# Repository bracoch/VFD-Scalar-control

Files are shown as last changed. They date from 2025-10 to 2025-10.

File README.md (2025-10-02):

Frequency Converter Design – Final Thesis Project
📌 Overview

This project was developed as part of my final thesis in Electrical Engineering.
The goal was to design and implement a complete frequency converter for asynchronous motor control, covering the full engineering cycle from concept to validation.

⚙️ Key Features

Power Stage Design – dimensioning of rectifier, DC link, and inverter section

Control Algorithms – PWM generation, Scalar V/f control

System Simulation – MATLAB/Simulink models for power electronics

Hardware Prototyping – schematic design and PCB layout

Testing & Validation – practical measurements, analysis and performance

🛠️ Technologies Used

MATLAB/Simulink – modeling and simulation

ISIS / Proteus - modeling and simulation

EasyEda PCB – schematic capture and PCB design

Arduino – microcontroller control logic

Oscilloscope & Measurement Tools – signal and harmonic analysis

📊 Results

Achieved SCALAR V/F stable motor control from 0–70 Hz

Verified power stage design through thermal and efficiency measurements

Implemented protection features (overcurrent, undervoltage, overvoltage)

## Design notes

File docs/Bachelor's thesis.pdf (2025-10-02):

## Faculty of Technical Sciences in Čačak

## University of Kragujevac

# Scalar Control of Three-Phase Induction Motor Characteristics

## Bachelor Thesis

Aleksandar Brakocevic | Thesis Supervisor
1220/17 | PhD Milan Dobricic

___________________________ ___________________________

SUMMARY

Alternating current (AC) motors are usually controlled by variable frequency drives (VFD), which regulate motor speed by adjusting the frequency of the supply voltage. Depending on the application and the required level of speed regulation, VFDs can be controlled using scalar or vector methods. The most common type of VFD control is scalar, which applies the volts-per-hertz (V/Hz) or volts-per-frequency (V/F) method.
The terms variable frequency drive (VFD) and variable speed drive (VSD) are often used interchangeably, but there is a difference between the two. A variable speed drive (VSD) is any drive that can control the speed of a piece of equipment, including both AC and DC motors. VSDs may operate through mechanical, hydraulic, or electrical drives. A variable frequency drive (VFD), on the other hand, is specifically used to control the speed of AC motors by varying the frequency of the motor supply voltage.
How does V/Hz control work?
AC motors are designed to operate with a constant magnetic field (flux). The strength of this magnetic field is proportional to the ratio of voltage (V) to frequency (Hz), or V/Hz. The VFD controls the motor speed by varying the frequency of the applied voltage, according to the synchronous speed equation:

Ns =

120 ∗ f
p
where:
- ns= synchronous speed (in revolutions per minute, rpm)
- f = supply frequency (in hertz, Hz)
- P = number of motor poles

Changing the frequency of the voltage affects both the motor speed and the strength of the magnetic field. When the frequency is reduced (for lower motor speeds), the magnetic field increases, creating excessive heat. When the frequency is increased (for higher motor speeds), the magnetic field decreases, resulting in lower torque. To maintain a constant magnetic flux, the V/Hz ratio must remain constant. The V/Hz method keeps torque generation stable regardless of frequency. V/Hz control of a VFD avoids changes in the strength of the magnetic field by adjusting the voltage together with the frequency so that the V/Hz ratio remains constant.

The appropriate V/Hz ratio is determined by the rated voltage and frequency of the motor. For example, a motor rated for delta connection at 230 V and 50 Hz will always operate best with a V/Hz ratio of 4.6 (230/50 = 4.6).

Open-loop (V/Hz) control does not use feedback and only adjusts the voltage and frequency of the motor based on an external speed command.
Closed-loop V/Hz control can incorporate encoder feedback to measure the actual motor speed. An error signal is generated based on the difference between the actual speed and the reference speed, and the controller produces a new frequency command to compensate for the error. Although closed-loop V/Hz improves speed regulation, it is not commonly used because of the additional cost and complexity of the feedback hardware.

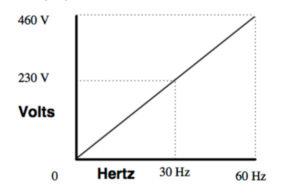
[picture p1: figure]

Figure 1.
V/Hz regulation maintains a constant ratio between voltage (V) and frequency (Hz).

V/Hz control is a simple and low-cost method for operating variable frequency drives and is generally considered the most common VFD control scheme. It is suitable for both constant-torque and variable-torque applications and can provide up to 150 percent of rated torque at zero speed for starting and peak loads. Speed regulation is typically within 2 to 3 percent of the maximum rated frequency, making this method unsuitable for applications where precise speed control is critical.

The most common use of V/Hz control is for driving industrial equipment such as fans and compressors. A unique advantage of V/Hz control over other methods is that it allows multiple motors to be operated from a single VFD. All motors will start and stop simultaneously and run at the same speed, which is beneficial in some process applications such as heating and cooling.

Contents:

6. Microcontroller Program | Error! Bookmark not defined.
6.2 Program Flow | Error! Bookmark not defined.

Appendix 1. Output Stage Schematic | Error! Bookmark not defined.

Appendix 4. Printed Circuit Board Layout (Top Side)* .... Error! Bookmark not defined.

Appendix 10. Parts List | Error! Bookmark not defined.

### 1. PREFACE

The final thesis represents a seal on the previously acquired knowledge that was selflessly imparted to us by our professors during lectures. Likewise, this work I have chosen to pursue is an attempt to leave a positive impression on the professors and to justify the time they dedicated to us, striving to bring us closer to the subject matter and prepare us for future endeavors.
I have spent a great deal of time working on this thesis, but that time is nothing compared to the knowledge I have gained, both theoretical and especially practical, during its realization. Each stage of the work brought new positive experiences as well as disappointments, particularly when things did not go the way I had hoped. As the saying goes: “Electronic components run on white smoke—when the smoke escapes, the component no longer works.” I too have witnessed plenty of white smoke, but perseverance paid off, and I successfully completed the project. The feeling and satisfaction of having accomplished something independently and with full understanding is unparalleled.
I would like to express my deep gratitude to Professor Dr. Milan Dobričić, Professor Dr. Dragan Brajović, and Professor Dr. Božimir Mišković.

Aleksandar Brakočević
September 2021

### 1.1 INTRODUCTION

Induction motors are the most commonly used motors. They are robust, reliable, and durable. When voltage is applied to an induction motor according to the specifications on its nameplate, the motor runs at its rated speed. However, in many applications, variable speed operation is required. For example, a washing machine may use different speeds for each wash cycle. Historically, mechanical gear and belt systems were used to achieve variable speeds. Thanks to the rapid advancement of electronics, power and control systems have matured to the point where these components are now used to control motors instead of mechanical gears. Electronics not only control motor speed but can also improve the dynamic performance of the motor. Additionally, electronics can reduce the system’s average power consumption and lower motor noise.
Controlling an induction motor is complex because of its nonlinear characteristics. Although different control methods exist, the variable voltage variable frequency (VV/VF) or V/F method is the most common speed control method in open-loop systems. This method is most suitable for applications that do not require position control or high-precision speed regulation. Examples include heating, air conditioning, fans, and compressors.
V/F control can be implemented using inexpensive microcontrollers instead of costly processors and digital signal processors (DSP). Many microcontrollers have built-in hardware PWM (pulse width modulation) signal generators. The Arduino Mega development board is equipped with an ATmega2560 microcontroller, which contains six timers and fifteen PWM pins that can be configured in the corresponding registers for different signal values. In this work, we use three PWM pins to generate three SPWM (sine pulse width modulation) signals phase-shifted by 120°.

This thesis covers the basics of scalar control of three-phase induction motors.

### 1.2 Nameplate

A typical nameplate (Figure 1) of an induction motor contains the following parameters:
- Rated supply voltage at the terminals in volts (V)
- Supply frequency in hertz (Hz)
- Rated current in amperes (A)
- Base speed in revolutions per minute (RPM)
- Power in watts or horsepower (kW–HP)
- Rated torque in newton-meters (Nm)
- Slip speed in RPM, or slip frequency in hertz (Hz)
- Type of winding insulation – class A, B, F, or H
- Efficiency
- Type of stator connection (for three-phase motors only), star (Y) or delta (Δ)

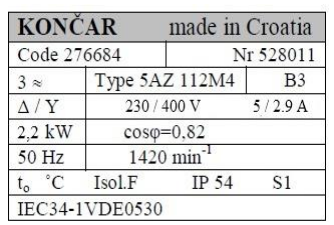
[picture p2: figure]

Figure 1. Motor Nameplate

### 1.3 Operating Principle of the Induction Motor

When rated alternating current supply is applied to the stator windings, a magnetic flux of constant magnitude is generated, rotating at synchronous speed. The rotating field moves in the air gap and closes through the stator and rotor, which induces corresponding electromotive forces in the conductors. In the stator winding, a counter electromotive force EsE is generated, which balances the applied stator voltage U. An electromotive force is also induced in the rotor winding. If the rotor circuit is closed, a current Ir will flow, whose active component has the same direction as the induced electromotive force. Since the conductor carrying the current IrI is located in a magnetic field, an electromagnetic force F acts on it, causing the rotor to turn in the direction of the rotating magnetic field. The sum of all the forces acting on the rotor conductors represents the electromagnetic torque of the motor.
As energy is transferred from the stator to the rotor by electromagnetic induction, asynchronous machines are often called induction machines. The windings are of resistive-inductive nature. Reactive energy is required to magnetize the magnetic material and the air gap between the stator and rotor. Since the asynchronous machine cannot generate reactive energy, it must draw it from the network. The current driven through the windings by the supply voltage will always be inductive. Therefore, the asynchronous machine, both in motor and generator mode, consumes reactive energy, which is one of the main reasons why it is used primarily as a motor. In generator mode, the asynchronous machine is used within autonomous power systems, where the reactive energy is supplied by a capacitor bank. In large industrial consumers with many high-power asynchronous motors, static compensators (usually capacitor banks) are often installed to improve the power factor so that reactive energy is not drawn from the network.
To reduce the relative speed, the rotor begins to rotate in the same direction as the flux and attempts to catch up. But in practice, the rotor can never “reach” the stator field. Thus, the rotor always runs slower than the speed of the stator field. This difference in speed is called slip speed, and it depends on the mechanical load on the motor shaft.
The frequency and speed of the motor, with respect to the input supply, are referred to as the synchronous frequency and synchronous speed. The synchronous speed is directly proportional to the ratio of the supply frequency to the number of poles in the motor. The synchronous speed of the induction motor is shown in Equation (1.1).

synchronous speed Ns =

120 ∗f
p
f – rated supply frequency | (1.1)
p – number of poles

Synchronous speed is the speed at which the stator flux rotates. The rotor flux rotates slower than the stator flux. This difference is called slip speed. The speed indicated on the motor nameplate is the base speed. Some manufacturers specify it as a percentage of synchronous speed, as shown in Equation (1.2):

Nk% =

(Ns−Nn) ∗100 Ns | (1.2)

where:
- Nn_= base speed
- Ns = synchronous speed
- Nk = slip speed

The slip percentage depends on the motor load: the higher the load, the greater the slip.

### 1.4 Types of asynchronous motors

Based on rotor construction, induction motors are classified into two categories:

- squirrel-cage motors
- slip-ring motors

The stator construction is the same for both types.

### 1.5 Squirrel-cage rotor motor

Almost 90% of asynchronous motors are squirrel-cage motors. This is because the squirrel-cage motor has a simple and robust construction. The rotor consists of a cylindrical laminated core with axially placed parallel slots to hold the conductors. Each slot is filled with copper, aluminum, or an alloy. The rotor bars are short-circuited by end rings on both sides, as shown in Figure 2. The rotor slots are not parallel to the shaft; they are skewed for two main reasons:

a) To ensure quiet motor operation by reducing magnetic noise.
b) To help reduce the tendency of the rotor to lock..

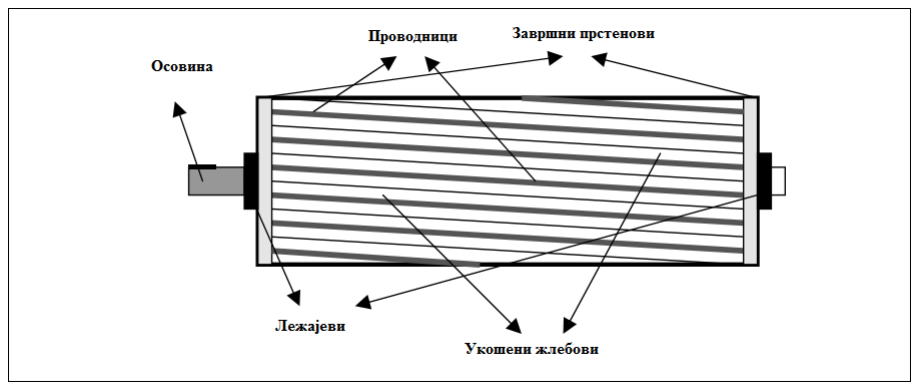
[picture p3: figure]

Figure 2. View of a squirrel-cage rotor

### 1.6 Slip-ring motor

The windings on the rotor are connected to three insulated slip rings on which brushes are mounted (Figure 3). This allows an external resistor to be introduced into the rotor winding. The external resistor can be used to increase the motor torque and modify the torque characteristics. Under normal operating conditions, the slip rings are short-circuited by an external switch. In normal conditions, the slip-ring motor operates like a squirrel-cage motor.

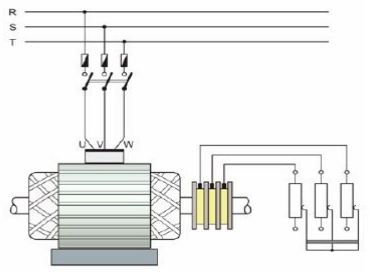
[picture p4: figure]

Figure 3. Slip-ring motor

### 1.7 Equivalent circuit of an asynchronous motor

The phasor model of the asynchronous motor, considering the steady-state motor quantities, is often used in the scalar control method. Before deriving the motor model, several assumptions are made:

- the stator windings are identical and sinusoidally distributed,
- the magnetic system is linear.

The voltage equations (2.1 and 2.2), with respect to the machine variables, can be expressed as:

V R I j s | s s | e s = | + ωλ | (2.1)
0 = | + R I j r r | | s r ωλ

Where Vs
| | | is the stator voltage vector,
s

I
is the stator current vector,

λs
is the stator leakage

flux vector,
r

I
is the instantaneous rotor current vector,

λr
is the rotor leakage flux vector,

ωe

is the synchronous speed,

ωr
is the rotor electrical speed, and
ω ω ω s | e | r
| =−
is the slip speed. | (2.2)

For a magnetically linear system, the leakage flux vector is calculated as follows (equations 2.3 and 2.4).
λs | s s | m r = | + L I L I
Stator leakage flux | (2.3)
λr | m s | r r = | + L I L I
Rotor leakage flux | (2.4)

In the above equations,

Rs
is the stator resistance,

Rr
is the rotor resistance,

mL
is the mutual

inductance,

s L
is the stator inductance, and

r L
is the rotor inductance.

In Figure 4, the equivalent circuit of the asynchronous motor is shown.

L | L L ls | s | m = | −
is the stator

leakage inductance,

L | L L lr | r | m = | −
is the rotor leakage inductance,, а s = ωs / ωe

/

### s e s =ωω

is

the | slip | ratio.

Figure 4. Equivalent circuit of the asynchronous motor

According to equations (3.1) ~ (3.4), the stator voltage and current are related by the equation:

( | )
( | )
( | )
2 | 2 | 2 | 2 2
2 | 2 2 | 2
s | e M | r | s | r | s | s r | r M
s | s | s | e s
r | s r | r | s r
LR | L R | L L | L L
V | R | I | j | I
R | L | R | L
ωω | ω
ω
| ω | | | | | ω
æ | ö | + | −
= | + | + ç | ÷ ç | ÷ + | + è | ø
(2.5)

And the stator leakage flux can be expressed as:
( | )
( | )
2 | 2 | 2 | 2

2 2

s | r | s | s r | r M | s | r M
s | s
r | r | s
L R | L L | L L | j R L
I
| R | L
ω | ω
λ
ω
+ | − | −
=
| +

(2.6)

Figure 5 shows the vector diagram of the motor quantities when the asynchronous motor operates in motoring mode..

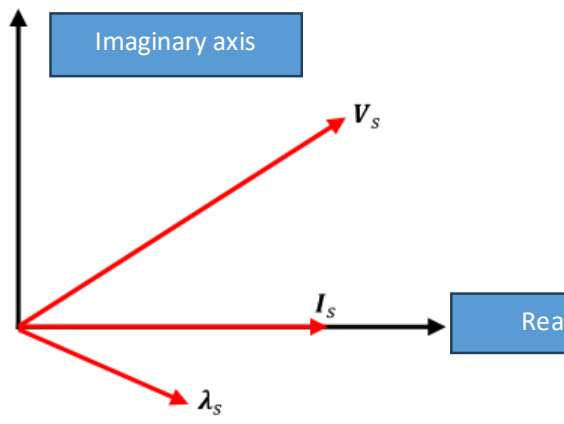
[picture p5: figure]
Imaginary axis

Figure 5. Vector diagram of motor quantities To describe an induction motor with P (number of) pole pairs, the generated torque can be expressed in terms of current and voltage as shown in equations (2.7) and (8.8).

2
2
2 | 2 | 2

3
*
2
M | r | s
e | S
r | r | s
P | LR T | I
R | L

ω
ω

=
+

(2.7)

( )

2
2
| 2
2 | 2 2

3
*
2
M | r | s | s
e
e
s | r | s | e | M | s r | r | s
P | L R | V T
R R | L | L L | R L
| | ω
ω ωω

=
é | ù + | − | + ê | ú ë | û

(2.8)

Where |x| denotes the magnitude of a vector. By neglecting the stator resistance, equation
(2.8) can be simplified and expressed by the following relation (2.9).

2
2
2 | 2 | 2 | 2 2

3
*
2 | ( | )
M r | s | s
e
s | M | s r | r | s | e
P | L R | V T
L | L L | R L
| ω
ω | ω

=
− +

(2.9)

Real axis

### 1.8 Torque–speed characteristic of asynchronous motors

Figure 6 shows the typical torque characteristics of an asynchronous motor. The X-axis represents speed and slip, while the Y-axis shows torque and current. The characteristics are drawn at the rated voltage and frequency supplied to the stator.
During startup, the motor usually draws up to seven times the rated current. This high current is the result of the stator and rotor flux, stator and rotor losses, winding losses, and bearing friction losses. This large starting current overcomes these losses and produces torque on the rotor, causing it to begin rotating.
At startup, the motor delivers about 1.5 times the rated torque of the motor. This starting torque is also called the locked-rotor torque (LRT). As the speed increases, the current drawn by the motor decreases slightly (see Figure 6).

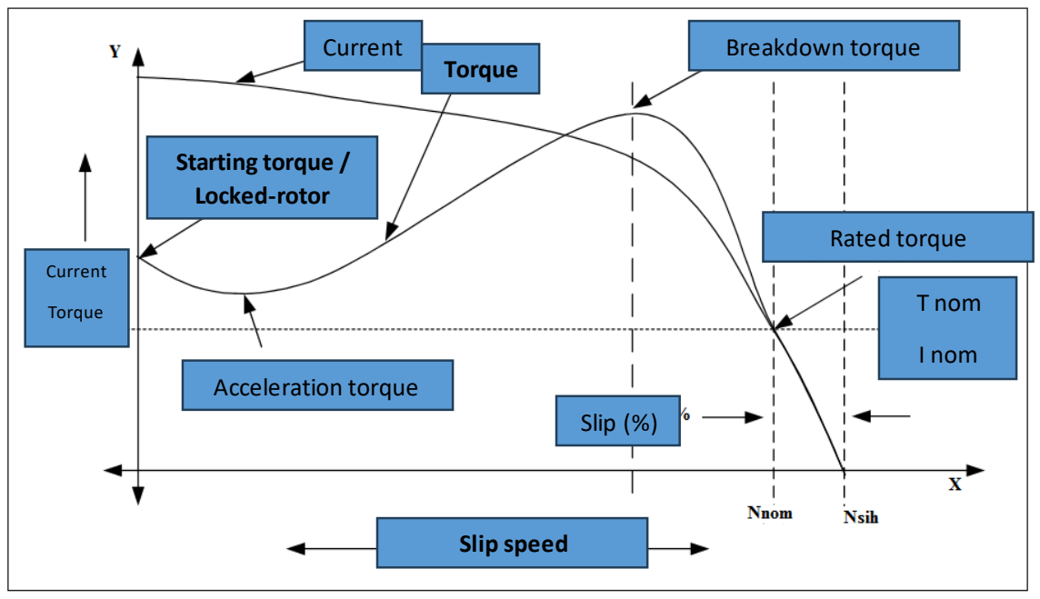
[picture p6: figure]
Current; Torque; Starting torque / Locked-rotor; Acceleration torque; Breakdown torque; Rated torque; Slip (%); Slip speed; T nom; I nom

Figure 6. Torque–speed characteristic of an asynchronous motor

The current decreases significantly as the motor speed approaches ~80% of the rated speed. At the rated speed, the motor draws the rated current and delivers the rated torque.

At rated speed, if the load on the motor shaft is increased beyond the rated torque, the speed begins to drop and the slip increases. When the motor operates at approximately 80% of synchronous speed, the load can be increased up to 2.5 times the rated torque. This torque is called the breakdown torque. If the load on the motor continues to increase, the motor will stall.

Furthermore, when the load exceeds the rated load, the load current increases. Due to this higher current flow in the windings, the winding losses also increase, which leads to a rise in the motor winding temperature. Motor windings can withstand different temperatures depending on the insulation class and the motor cooling system. Some motor manufacturers provide overload and duty cycle data. If the motor is overloaded longer than recommended, it may burn out.

As can be seen from the torque characteristics, the torque is highly nonlinear as the speed varies. In many applications, the speed needs to be varied, which makes the torque variable. In this work, we will address a simple speed control of the asynchronous motor using the V/F method in open loop, also known as scalar control.

### 2. Scalar control

As can be seen from the torque characteristics, the asynchronous motor draws the rated current and delivers the rated torque at the base speed. When the load increases (overload), the speed decreases and the slip increases. As mentioned in the earlier section, the motor can take up to 2.5 times the rated torque with a speed drop of about 20%. Any further increase in the shaft load can stall the motor.
The torque developed by the motor is directly proportional to the magnetic field produced by the stator. Therefore, the voltage applied to the stator is directly proportional to the product of the stator flux and the angular speed. This makes the flux produced by the stator proportional to the ratio of the applied voltage to the supply frequency.
By varying the frequency, the motor speed can be changed. Hence, by varying both the voltage and the frequency in the same ratio, the flux—and therefore the torque—can be kept constant over the entire speed range. (3.1)

Stator voltage (V) ∝ [Stator flux (ϕ)] * [Angular speed (ω)]
V ∝ ϕ*2πF | (3.1)
ϕ ∝

V
f

In Figure 7, the relationship between voltage and torque with respect to frequency is shown. The Y-axis represents voltage, and on the X-axis the frequency increases up to the rated speed. At the rated speed, both voltage and frequency reach their rated values specified on the nameplate.
We can force the motor to operate above its rated speed by increasing the frequency. However, the voltage cannot be increased above the rated voltage. Therefore, only the frequency can be increased, which results in field weakening and a reduction of the available torque.
Above the rated speed, losses increase significantly, and thus the torque curve becomes nonlinear with respect to speed or frequency.

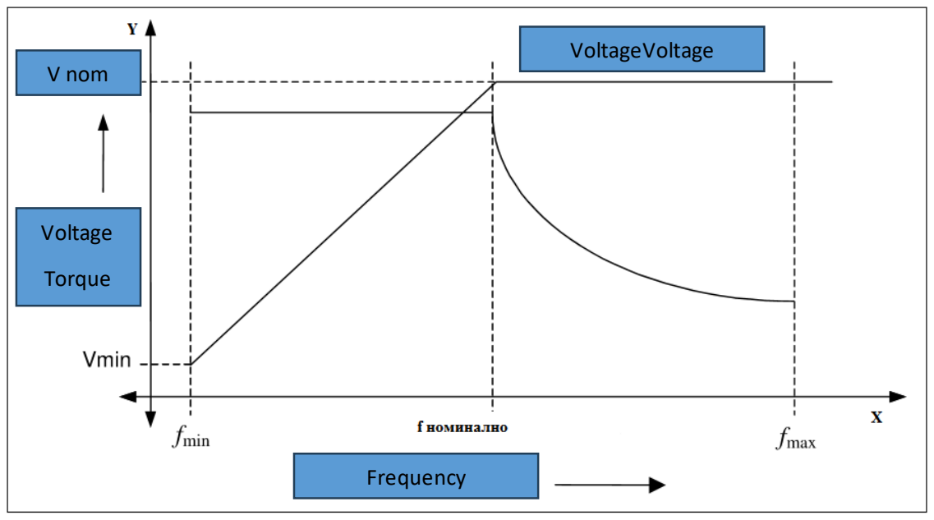
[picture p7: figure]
Frequency; VoltageVoltage; V nom; Voltage; Torque

Figure 7. Relationship of voltage and torque with respect to frequency

### 3. Implementation

### 3.1 Output IGBT stage

A 3-phase asynchronous motor is connected to a 3-phase bridge inverter as shown in Figure 8. The power inverter consists of six IGBT transistors, controlled by a microcontroller to generate a three-phase AC output from a DC source. PWM signals generated by the microcontroller control these six transistors.
The transistors IGBTH1 to IGBTH3, connected to DC+, are called the upper switches. The transistors IGBTL1 to IGBTL3, connected to DC–, are called the lower switches. The amplitude of the phase voltage is determined by the duty cycle of the PWM signals. While the motor is running, three out of the six switches will be on at any given time—either one upper and two lower switches, or one lower and two upper switches.
By alternately switching certain groups of transistors, a rectangular voltage waveform rich in harmonics (caused by the PWM switching frequency) is generated. The inductive nature of the motor stator windings filters this current to produce a three-phase sinusoidal waveform with negligible harmonics.
When the transistors are turned off, the inductive nature of the windings resists any sudden change in current flow until all the energy stored in the windings is released. To facilitate this, ultra-fast diodes are provided across each transistor. These diodes are known as freewheeling diodes or flyback diodes.
To prevent a short circuit of the DC source, the upper and lower transistors of the same half-bridge must never be turned on simultaneously. This is achieved by inserting a dead time when switching transistors in the same half-bridge branch, either through software programming of the PWM registers or by using specially designed driver circuits with built-in dead time. The typical dead time ranges from 100–500 ns. One such circuit, used in this project, is the IR2109 driver IC from Infineon Technologies.

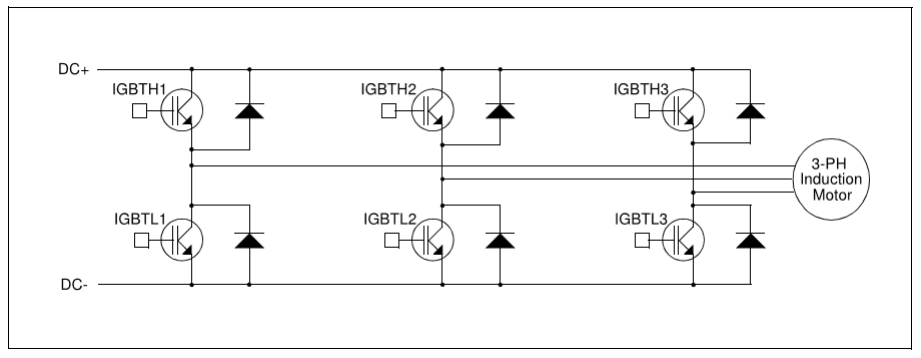
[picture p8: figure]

Figure 8. Drive output stage with IGBT transistors

### 3.2 Control of the output stage

As mentioned earlier, the Atmega 2560 microcontroller has 15 PWM outputs, each of which can be controlled independently to generate three independent PWM signals phase-shifted by 120° using the SPWM technique, which will be described later. In this example, we use Timer 5 of the microcontroller, which is configured to operate in PWM mode. The frequency is set by writing a specific combination into the PWM registers of the microcontroller. A detailed description of the configuration is provided in the appendix of the application program, written in the “ARDUINO” development environment, and included on the CD attached to this work.
To generate a variable three-phase AC voltage from a DC source, six PWM signals are required to control the output transistors individually. Since we are using only three PWM pins of the microcontroller, with the help of IR2109 IGBT drivers we generate all six signals to drive the IGBT transistors. The IR2109 IC has only one input, to which a single PWM pin of the microcontroller is connected. Inside the IC, its control logic generates complementary output signals for the upper and lower switches of the half-bridge, with built-in dead time. Thus, with one input signal, the IR2109 drives both transistors of the half-bridge, and the same applies to the remaining two half-bridge legs. In total, three IR2109 IGBT drivers are required.

### 3.3 BOOTSTRAP supply of the upper output transistors

One of the most commonly used methods for powering the current circuit of the upper output driver transistors is the BOOTSTRAP supply. The BOOTSTRAP supply consists of a BOOTSTRAP diode D1 and a BOOTSTRAP capacitor C1 (Figure 9). The advantage of this method is its simplicity and low cost. The maximum voltage that the bootstrap capacitor (VBS) can reach depends on the components used in the bootstrap supply circuit.

### 3.4 Bootstrap capacitor calculation

The BOOTSTRAP capacitor must be chosen so that it delivers enough energy to reliably turn on the upper output transistor without discharging excessively. In practice, the value of the bootstrap capacitor is taken to be about 10 times the gate capacitance of the upper output transistor (Cg) to ensure sufficient supply and a steady current during one PWM cycle.
The calculation of Cg is based on the gate drive supply voltage for the high-side IGBT—i.e., the gate-emitter voltage (Vge)—and the gate charge time (Qg).
In this work, the approximate voltage (Vge) can be expressed by the following equation (3.2).

15 VGE VDD VDboot | V ≈ | − | = | − ≈ 13.3 1 12.3 | (3.2)
VDD- Supply voltage of the driver stage
VDboot- Voltage drop across the bootstrap diode

The IGBT transistor HGTG20N60 has Qg = 142 nC according to the datasheet, so the equivalent gate capacitance would be, according to equation (3.3)

7
*

1

142 | *12.3 | 142C*10 *12.3 | 1.74
10* | 17.4
g | g | GE
| | g
C | Q V | nC | V | V | F
C | C | F | | | µ
| | µ

−
= | = | = | =
≥ | =

(3.3)

### 3.5 Gate protection and discharge circuit

The gate discharge circuit is designed with fast diodes 1N4148 (D2–D4), resistors R1–R4, and resistors R3–R6. The gate charging is carried out through resistors R2–R5. Gate overvoltage protection (Vge) is provided by Zener diodes D3–D5 rated at 15 V.

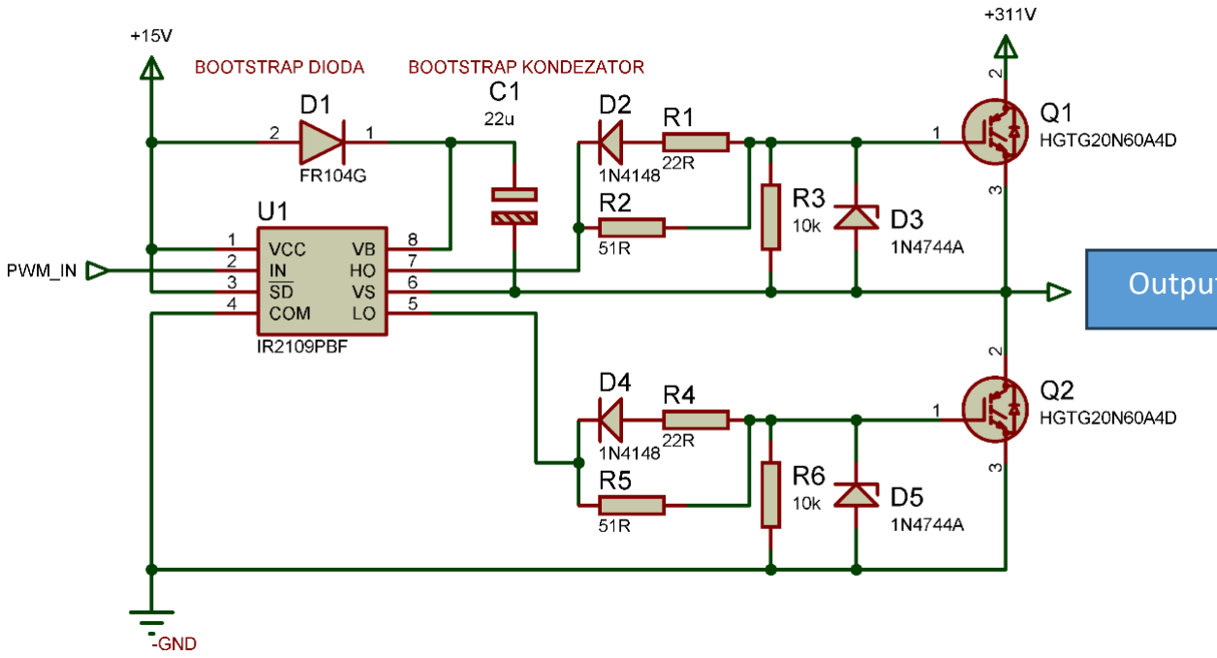
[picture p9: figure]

Figure 9. Driver and output stage

### 3.5 Power supply

The power supply of the frequency converter is 220 V–50 Hz. The voltage is rectified by a diode bridge in a Graetz connection, with a resistor limiting the initial charging current of the capacitor. After a time delay defined in the microcontroller program, a relay switches on, bypassing the resistor and applying full voltage to a 470 µF capacitor, which filters the rectified voltage and forms a DC voltage of 311 V for the power stage.
Additionally, there is another rectifier 220 V / 13.3 V / 5 V for supplying the microcontroller (+5 V) and the output stage (+13.3 V) (Figure 10).

Output phase

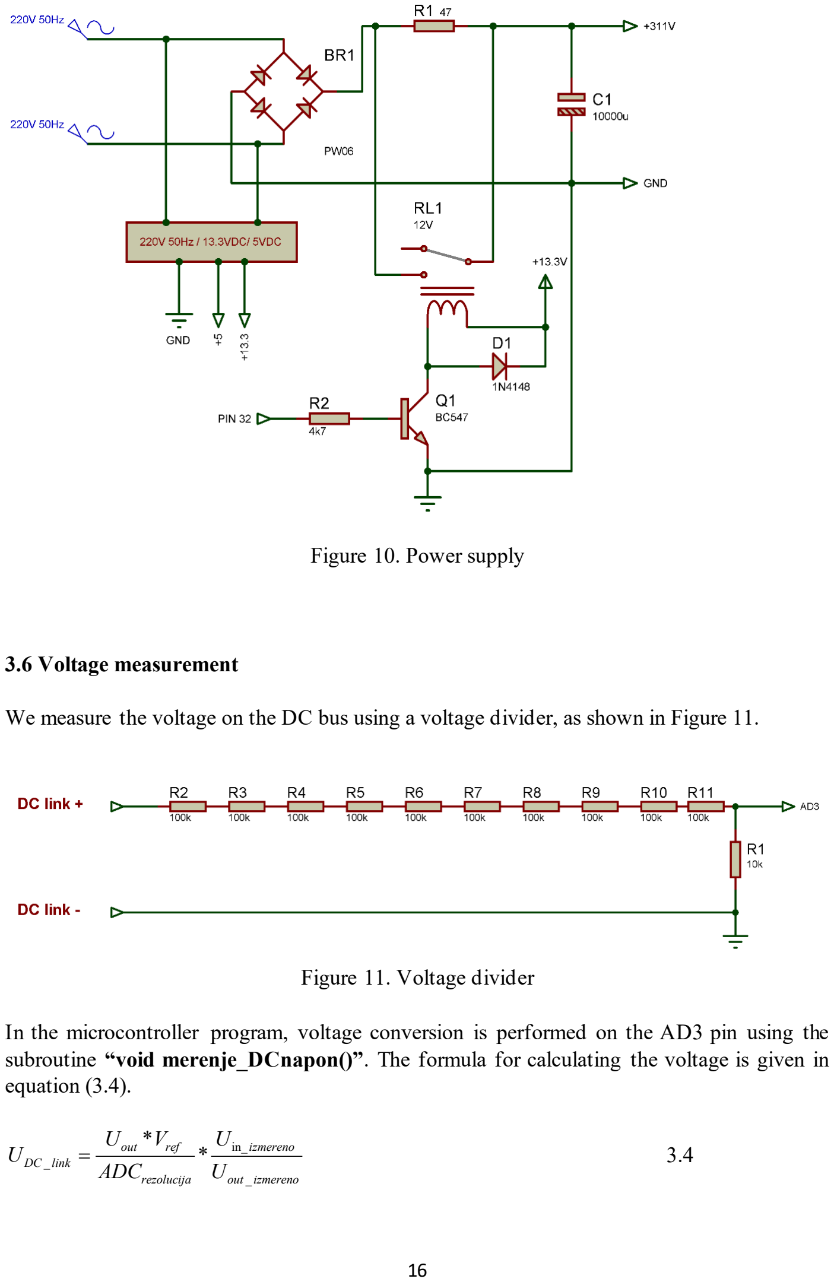
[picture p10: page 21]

Figure 10. Power supply

### 3.6 Voltage measurement

We measure the voltage on the DC bus using a voltage divider, as shown in Figure 11.

Figure 11. Voltage divider

In the microcontroller program, voltage conversion is performed on the AD3 pin using the subroutine “void merenje_DCnapon()”. The formula for calculating the voltage is given in equation (3.4).

in_
_
_

*
*
out | ref | izmereno
DC link
| rezolucija | out izmereno
U | V | U
U
ADC | | U
= | 3.4

### 3.7 Current measurement

Current measurement is carried out using the Arduino ACS712 current sensor module. In this work, only one phase of the motor is measured, and the current value is sampled every 20 ms on the AD2 pin of the microcontroller. If the current exceeds the preset value, the motor is stopped. The circuit diagram is shown in Figure 12, and the module is shown in Figure 13.

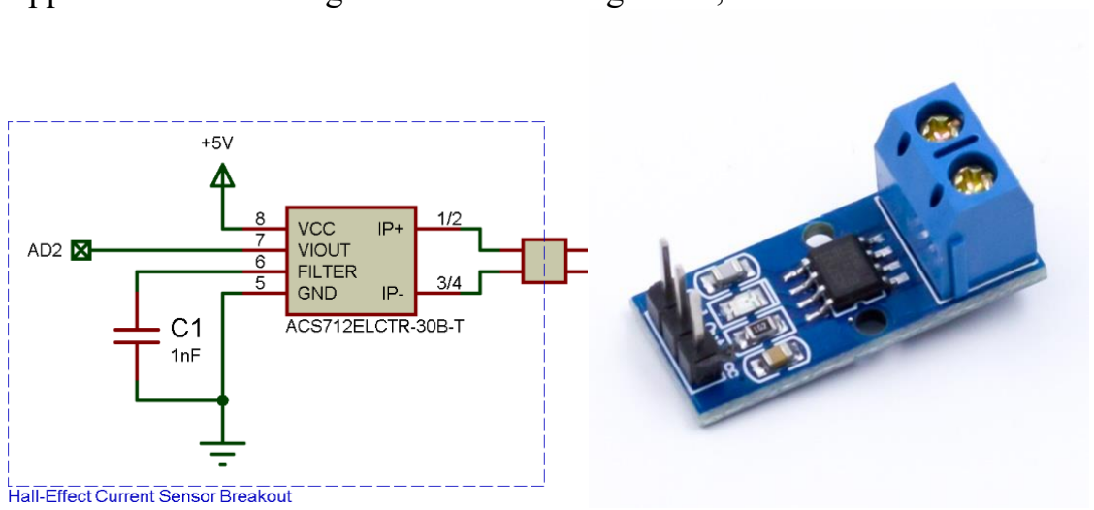
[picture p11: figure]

Figure 12. ACS712 circuit diagram Figure 13. Arduino ACS712 module

The subroutine that performs current measurement uses a preinstalled library specifically designed for the ACS712 module and is included with this work on the attached CD. The library is called <ACS712.h>.

### 4. ARDUINO MEGA – microcontroller

### 4.1 Schematic of the Arduino Mega development board (Figures 13, 14, 15)

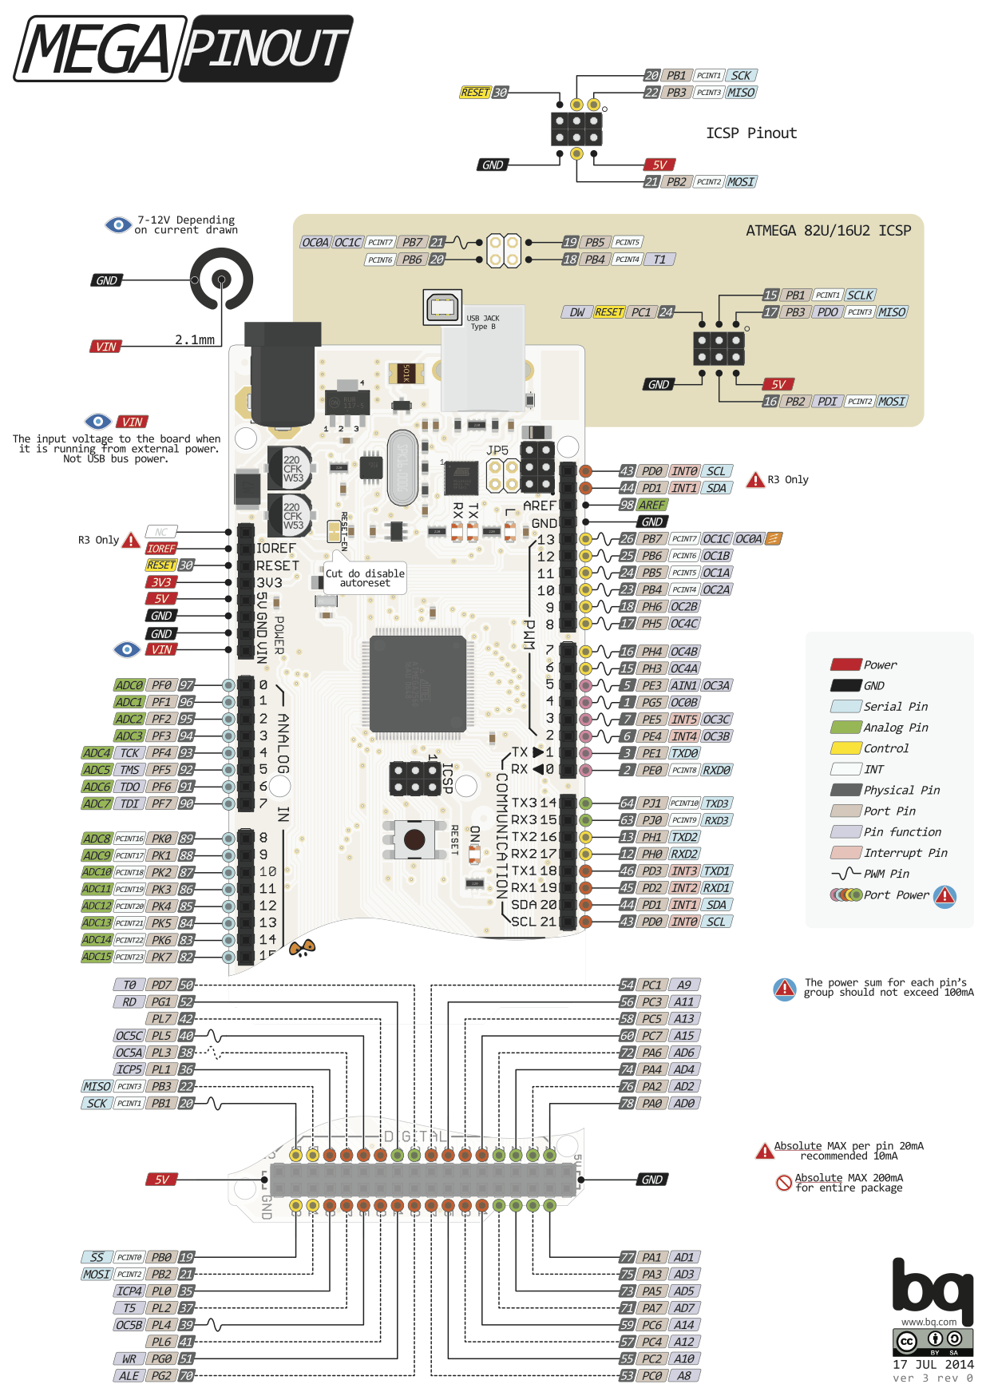
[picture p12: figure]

Figure 13.

Figure 14.

Gigure 15.

### 4.2 Controller Specifications

Microcontroller------------------------------ATmega2560 Operating Voltage----------------------------5V
Input Voltage (recommended)------------------7-12V
Input Voltage (limits)-----------------------6-20V
Digital I/O----------------------------------54 (of which 15 can be used as PWM outputs) Analog Inputs--------------------------------16
DC Current per I/O Pin-----------------------40 mA
DC Current for 3.3V Pin----------------------50 mA
Flash Memory---------------------------------256 KB (8 KB used by bootloader) SRAM-----------------------------------------8 KB EEPROM---------------------------------------4 KB
Clock Speed----------------------------------16 MHz

### 4.3 Digital pins

Pin
Digital Pin 0-------------------------------------RXD0 (Serial Port 0) Digital Pin 1-------------------------------------TXD0 (Serial Port 0) Digital Pin 2-------------------------------------External Interrupt 0 - PWM Digital Pin 3-------------------------------------External Interrupt 1 - PWM Digital Pin 4-------------------------------------PWM
Digital Pin 5-------------------------------------PWM
Digital Pin 6-------------------------------------PWM
Digital Pin 7-------------------------------------PWM Digital Pin 8-------------------------------------PWM Digital Pin 9-------------------------------------PWM Digital Pin 10------------------------------------PWM
Digital Pin 11------------------------------------PWM
Digital Pin 12------------------------------------PWM
Digital Pin 13------------------------------------Built-in LED - PWM Digital Pin 14------------------------------------TXD (Serial Port 3) Digital Pin 15------------------------------------RXD (Serial Port 3)
Digital Pin 16------------------------------------TXD (Serial Port 2)
Digital Pin 17------------------------------------RXD (Serial Port 2)
Digital Pin 18------------------------------------TXD (Serial Port 1) - External Interrupt 5 Digital Pin 19------------------------------------RXD (Serial Port 1) - External Interrupt 4 Digital Pin 20------------------------------------I2C - SDA - External Interrupt 3
Digital Pin 21------------------------------------I2C - SCL - External Interrupt 2
Digital Pin 22–43---------------------------------General Purpose I/O pins
Digital Pin 44------------------------------------PWM
Digital Pin 45------------------------------------PWM
Digital Pin 46------------------------------------PWM
Digital Pin 50------------------------------------MISO Digital Pin 51------------------------------------MOSI Digital Pin 52------------------------------------SCK Digital Pin 53------------------------------------SS

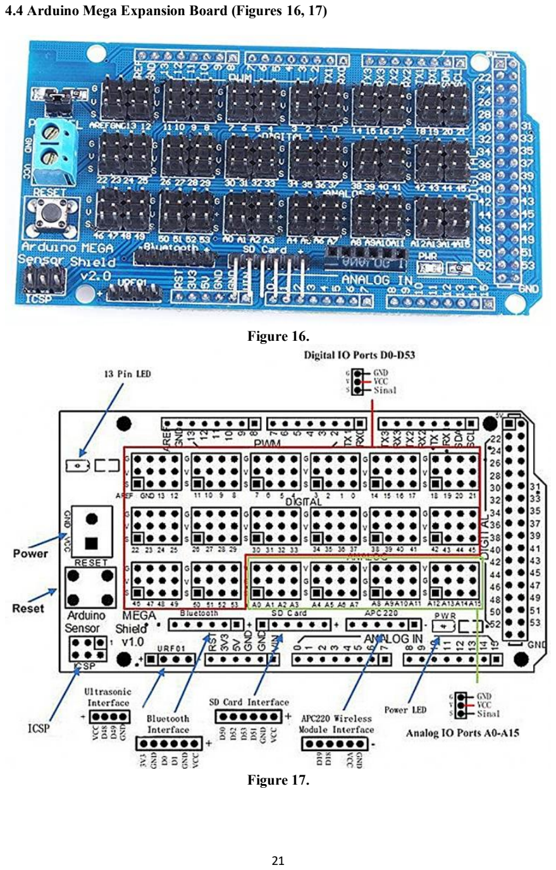
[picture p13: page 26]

### 4.4 Arduino Mega Expansion Board (Figures 16, 17)

Figure 16.

Figure 17.

### 5. SPWM (Sinusoidal Pulse Width Modulation) technique

By using Timer 5 of the microcontroller, we control the hardware PWM module to generate three independent PWM signals based on a sine table stored in the program memory of the microcontroller. After initialization at startup, the sine table is copied into the working memory of the microcontroller. In this way, the access time to the working registers of the microcontroller is reduced, and the operating characteristics of the three-phase motor are not affected. Each of the three PWM pins of the microcontroller has its own registers in which an offset is defined, and each of these registers points to a value in the table, such that they always maintain a phase shift of 120° with respect to each other.
Figure 18

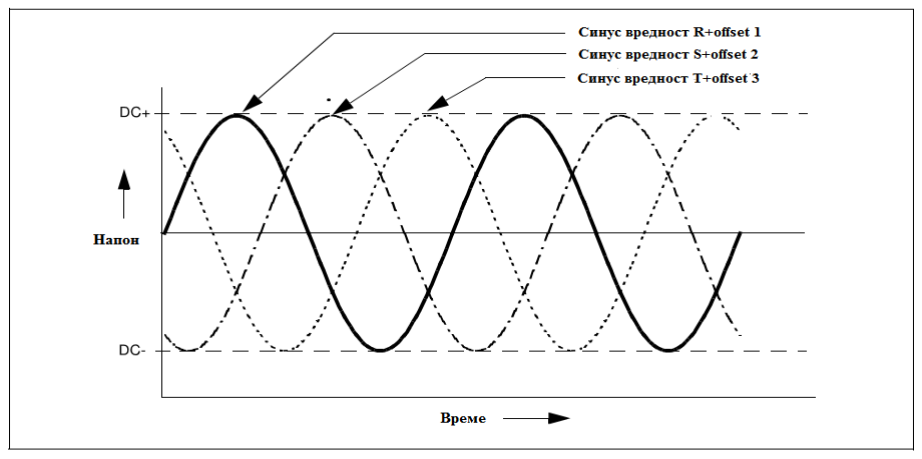
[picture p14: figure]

Figure 18. Генерисање трофазног синусног напона

A potentiometer connected to the 10-bit Analog-to-Digital Converter channel (AN0) determines the motor frequency. The microcontroller uses the converter results to calculate the duration of the PWM pulses, and consequently the amplitude and frequency of the motor. To ensure a smooth transition of frequency from higher to lower values and vice versa, the set frequency is read during each Timer 3 interrupt. The motor frequency value is controlled by Timer 1, which uses the result of the ADC to provide the preloaded value (preload value of the OCR1 register) at which the interrupt routine will occur, defined by the following relation: The required speed value in [Hz] is obtained by reading the Analog-to-Digital Converter channel (AN0), and depending on the potentiometer position, the corresponding frequency value is calculated (Equation 4.1).

freq = map(analogRead(FREQ_POT), POT_MIN, POT_MAX, FREQ_MIN, FREQ_MAX); (4.1) where is:
freq = value of the set (calculated) frequency;
FREQ_POT = ADC channel on the controller (in this case AN0);
POT_MIN = minimum ADC conversion value (0);
POT_MAX = maximum ADC conversion value (1023);
FREQ_MIN = minimum motor rotation frequency (7 Hz);
FREQ_MAX = maximum motor rotation frequency (7–70 Hz);
map = Arduino function for calculating the value within the previously defined limits;

Example of the map function for a frequency value of 50 Hz, equation (4.2) (FREQ_POT POT_MIN)* (FREQ_MAX FREQ_MIN)
_
(POT_MAX POT_MIN)
(1023 0)* (50 7) 7 50
(1023 0)
map | FREQ MIN

map

− | −
= | +
| −
− | −
= | + =
−

(4.2)

Timer 1 Settings:

register TCCR1A- (refer to Table 5 and Table 6)

Table 1. RegisterTCCR1A

Bit | 7 | 6 | 5 | 4 | 3 | 2 | 1 | 0
(0x80) | COM1A1 | COM1A0 | COM1B1 | COM1B0 | - | - | WGM11 | WGM10
READ/WRITE | R/W | R/W | R/W | R/W | R | R | R/W | R/W
Подешено у прогтраму | 0 | 0 | 0 | 0 | 0 | 0 | 0 | 0

Register TCCR1B- (refer to Table 5 and Table 6)

Table 2. RegisterTCCR1B

Bit | 7 | 6 | 5 | 4 | 3 | 2 | 1 | 0
(0x81) | ICNC5 | ICES5 | - | WGM13 | WGM12 | CS12 | CS11 | CS10
READ/WRITE | R/W | R/W | R | R/W | R/W | R/W | R/W | R/W
Подешено у прогтраму | 0 | 0 | 0 | 0 | 1 | 0 | 0 | 0

The required value for the Timer1 OCR1A register in order to obtain a frequency of 50 Hz is
calculated | using | the | following | equation | (4.3).
Since the sine table contains 39 predefined values, the time at which the interrupt routine will occur is calculated as follows:

int

int
int

int

1 | 1 | 0.02
50
0.02 | 512
_ | _ | _ | 39
1 | 1 | 1950
512
_ | 16000000 1 | 8205
* f | 1*1950
t | t | ms
Hz
t | ms
t | s
Sine uzoraka po ciklusu
f | | Hz
t
f osc | MHz OCR A
| prescaler

µ

= | → = | =
= | → | =
= | = | =
= | = | =

(4.3)

-f_osc = 16 MHz system clock of the microcontroller
-prescaler = in this example it is 1 (no division of the base frequency)

-map_result = value calculated by the microcontroller

-Sine_samples_per_cycle = number of predefined values in the sine table (39)

-tint = required interrupt time for the given frequency

-fint = interrupt frequency

-OCR1A = timer register responsible for the interrupt routine

After each Timer 1 interrupt (Figure 17), a value is read from three sine tables – one for each phase. The tables are formatted so that each has a phase shift of 120°. The value read from the tables is scaled based on the motor frequency. The sine table values are then multiplied by the amplitude register, which defines the PWM signal duration, and the calculated result is written into the OCR5A, OCR5B, and OCR5C registers of Timer 5, i.e., the PWM registers

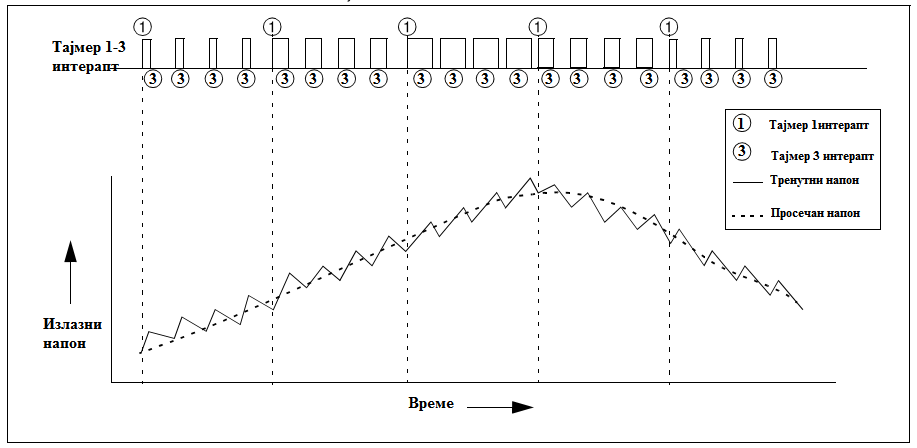
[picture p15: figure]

Слика 17. Timer 1 interrupt, PWM signal duration and voltage

The amplitude value of the PWM signal is calculated using equation (4.4). _
_ | _

zadata frekfencija Amp
nom frekfencija motora
= | (4.4)

In each interrupt routine, the amplitude value is checked, and if it is greater than 1, it is limited
to | 1.
After that, the PWM registers are updated for the next reading. If the button for changing the motor direction is pressed, the positions of the PWM_Soft_x registers are swapped, thereby achieving a phase shift, and the motor starts rotating in the opposite direction.
Direction 1: | Direction 2:
FAZA_U(OCR3A) = (PWM_Soft_A); | FAZA_U(OCR3A) = (PWM_Soft_A);
FAZA_V(OCR3B) = (PWM_Soft_B); | FAZA_V(OCR3B) = (PWM_Soft_C);
FAZA_W(OCR3C) = (PWM_Soft_C); | FAZA_W(OCR3C) = (PWM_Soft_B);

Timer 5 is set to a frequency of 6 kHz, which is also the PWM frequency, i.e., the switching frequency of the controller.
Timer 5 Settings:
Register TCCR5A: (see Table 5 and 6)

Table 3. Регистар TCCR5A

Bit | 7 | 6 | 5 | 4 | 3 | 2 | 1 | 0
(0x80) | COM5A1 | COM5A0 | COM5B1 | COM5B0 | COM5C1 | COM5C0 | WGM51 | WGM50
READ/WRITE | R/W | R/W | R/W | R/W | R/W | R/W | R/W | R/W
Подешено у прогтраму | 1 | 0 | 1 | 0 | 1 | 0 | 1 | 0

Register TCCR5B: (see Table 5 and 6)

Тable 4. Регистар TCCR5B

Bit | 7 | 6 | 5 | 4 | 3 | 2 | 1 | 0
(0x81) | ICNC5 | ICES5 | - | WGM53 | WGM52 | CS52 | CS51 | CS50
READ/WRITE | R/W | R/W | R | R/W | R/W | R/W | R/W | R/W
Подешено у прогтраму | 0 | 0 | 0 | 1 | 0 | 0 | 1 | 0

Timer 5 is configured to operate at a clock of 6 kHz.

The duration of a single pulse is

1 | 1 | 166
| 6000
t | s
f
= | = | = | µ

Since Timer 5 operates in phase correct mode, i.e., it counts from 0 up to the set value and then from the set value back down to 0, the required value of the ICR5 register is calculated according to equation (4.5).

_ | 16000000 5 | 166
*switchig_freq*2 | 8*6000*2
f osc | Mhz ICR
prescaler
= | = | = | (4.5)

Accordingly, the maximum value in the sine table can be 166, as shown in Program Code 1.

const byte PROGMEM sine[] [39]={ {1,4,9,16,24,34,45,57,70,83,96,109,121,132,142,150,157,162,165,166,165,162,157,150,142,132,121,109,96,83,70,57,45,34,24,16,9,4,1}, {132,142,150,157,162,165,166,165,162,157,150,142,132,121,109,96,83,70,57,45,34,24,16,9,4,1,1,4,9,16,24,34,45,57,70,83,96,109,121}, {121,109,96,83,70,57,45,34,24,16,9,4,1,1,4,9,16,24,34,45,57,70,83,96,109,121,132,142,150,157,162,165,166,165,162,157,150,142,132}, };
Program Code Excerpt 1. (Sine table values for three PWM signals)

Table 5. Timer Prescaler Setting
CSx2 | CSx1 | CSx0 | Опис
0 | 0 | 0 | Нема извора такта(тајмер/бројач заустављен)
0 | 0 | 1 | Такт/1 (без прескалера)
0 | 1 | 0 | Такт/8 (од прескалера)
0 | 1 | 1 | Такт/64 (од прескалера)
1 | 0 | 0 | Такт/256 (од прескалера)
1 | 0 | 1 | Такт/1024 (од прескалера)
1 | 1 | 0 | Спољни извор такта на Т1 пин. Clock on faling edge
1 | 1 | 1 | Спољни извор такта на Т1 пин. Clock on rising edge

Table 6. Description of bits for different timer operating modes

Mод | WGMx3 | WGMx2
(CTC1)

WGMx1
(PWMx1)

WGMx0
(PWMx0)
Режим рада | TOP | Тајмер
OCRxx

TOV1 Flag
Set on
0 | 0 | 0 | 0 | 0 | Normal | 0xFFFF | Immediate | MAX
1 | 0 | 0 | 0 | 1 | PWM, Phase Correct, 8-bit | 0x00FF | TOP | BOTTOM
2 | 0 | 0 | 1 | 0 | PWM, Phase Correct, 9-bit | 0x01FF | TOP | BOTTOM
3 | 0 | 0 | 1 | 1 | PWM, Phase Correct, 10-bit | 0x03FF | TOP | BOTTOM
4 | 0 | 1 | 0 | 0 | CTC | OCR1x | Immediate | MAX
5 | 0 | 1 | 0 | 1 | Fast PWM, 8-bit | 0x00FF | BOTTOM | TOP
6 | 0 | 1 | 1 | 0 | Fast PWM, 9-bit | 0x01FF | BOTTOM | TOP
7 | 0 | 1 | 1 | 1 | Fast PWM, 10-bit | 0x03FF | BOTTOM | TOP
8 | 1 | 0 | 0 | 0 | PWM, Phase and Frequency Correct | ICRx | BOTTOM | BOTTOM
9 | 1 | 0 | 0 | 1 | PWM, Phase and Frequency Correct | OCRxA | BOTTOM | BOTTOM
10 | 1 | 0 | 1 | 0 | PWM, Phase Correct | ICRx | TOP | BOTTOM
11 | 1 | 0 | 1 | 1 | PWM, Phase Correct | OCRxA | TOP | BOTTOM
12 | 1 | 1 | 0 | 0 | CTC | ICRx | Immediate | MAX
13 | 1 | 1 | 0 | 1 | (Reserved) | - | - | -
14 | 1 | 1 | 1 | 0 | FAST PWM | ICRx | BOTTOM | TOP
15 | 1 | 1 | 1 | 1 | FAST PWM | OCRxA | BOTTOM | TOP

### 5.1 Timing diagrams

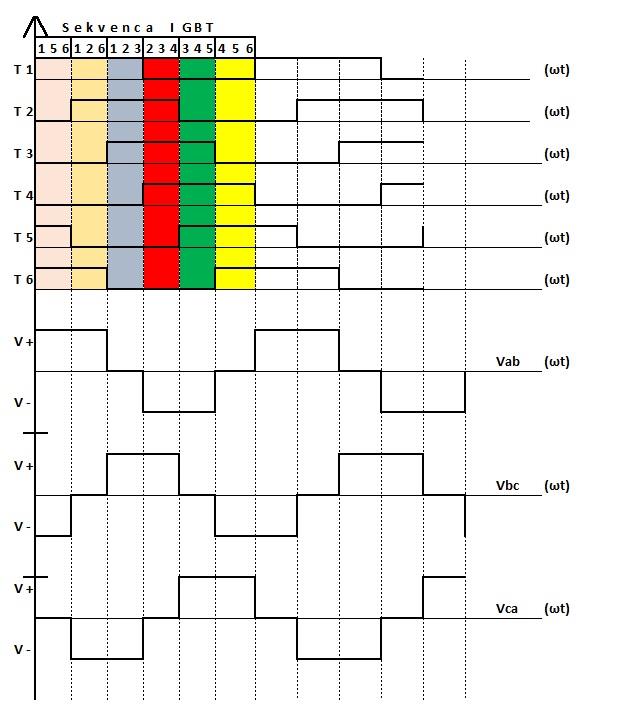
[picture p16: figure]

Figure 18. Conduction timing diagram at 180°

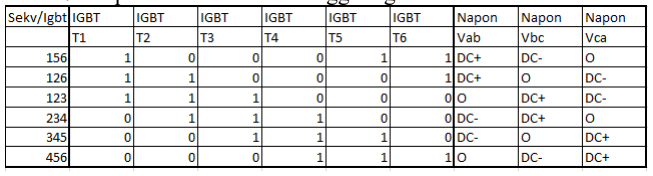
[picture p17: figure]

Table 7. Sequences of transistor triggering

### 6.3 Main program, subroutines, and interrupt routines

### 6.4 Main Program (void loop())

Here, subroutines are executed and called, key presses are checked, and the current values are displayed on the screen. The DC voltage value is monitored against predefined undervoltage and overvoltage limits, and if the voltage is outside the set range, the protection is triggered, stopping the motor and disconnecting the supply. The motor current is also monitored against the predefined nominal current value, and if the current exceeds the set value, the protection is activated and the motor is shut down. Auxiliary variables are created to generate timers for monitoring voltage and current, as well as for generating the animation that indicates the motor rotation direction. Timers are started to create interrupt routines for generating three-phase voltage using the PWM technique. The ADC0 value of the microcontroller is read to define the motor output frequency.

### 6.5 Subroutines

### 6.5.1 void citanje_tastera()

In this subroutine, the value of the microcontroller’s ADC1 is read, and by using buttons that change the resistance at the converter input, the button functions are defined, which are used to call various inverter functions. The buttons are defined in the following order:

-Тастер_Лево – button left
-Тастер_Десно – button right
-Тастер_Горе – button UP
-Тастер_Доле – button Down -Тастер_Стоп/Подешавање – utton Setup

### 6.5.2 void prikaz()

Here, the current and set values of frequency, voltage, current, etc. are displayed.

### 6.5.3 void Motor_stop()

It stops the motor, halts the timers and registers responsible for the controller operation, and sets the microcontroller registers to predefined values for a new controller start.

### 6.5.4 void podesavanje()

The condition for this subroutine to be called is that the controller is enabled and the motor is stopped.
The screen displays “STOP”, and by holding the Stop/Settings button for more than 2 seconds, the menu “SETTINGS” is entered.

Here, the following parameters are defined:

FREQ MAX OUT – maximum output frequency (30–70 Hz)
MOTOR CURRENT nom. – nominal motor current (0–20 A) ACCELERATION RAMP (sec) – motor run-up time in seconds (1–20 s) DECELERATION RAMP (sec) – motor stop time in seconds (1–20 s)
DC overvoltage – maximum DC voltage value
DC undervoltage – minimum DC voltage value
Motor frequency nom. – motor frequency from the nameplate (50 or 60 Hz)

By holding the Stop/Settings button for more than 2 seconds, the program returns to the main subroutine.

### 6.5.5 void brzina()

It calculates the required value for the Timer1 OCR1A register, which generates the interrupt routine responsible for the motor’s output frequency.

### 6.5.6 void merenje_DCnapon()

It is used for measuring the DC voltage (DC link voltage).

### 6.5.7 void pisanje__citanje_INT_eeprom

his subroutine is used for reading from and writing to the microcontroller’s EEPROM, and it is called during the controller startup and when exiting the “SETTINGS” subroutine.

### 6.6 Interrupt routines

### 6.6.1 ISR(TIMER1_COMPA_vect)

This is the Timer 1 interrupt routine, which is responsible for the output frequency value. It checks whether the stop button is pressed, verifies the rotation direction status, and updates the PWM registers by changing the positions of the sine table readings. The current sine table values, scaled by the amplitude register value, are written into the PWM registers of the microcontroller. At the end of the interrupt routine, the OCR1A register value of Timer 1 is always refreshed, and if necessary, the output frequency of the controller is increased or decreased.

### 6.6.2 ISR(TIMER3_COMPA_vect)

This Timer 3 interrupt routine is used for smooth deceleration or acceleration of the motor. During each Timer 3 interrupt, the controller frequency is increased or decreased (depending on the position of the frequency potentiometer) by 0.25 Hz until the set frequency is reached.

### 7. Operation with the controller

### 7.1 Power-up and System Initialization

Here, the initial values for the controller start are defined. After power is applied, the microcontroller sets the pins as inputs or outputs depending on the function of each pin defined in the program.

Input pins:
- AD0 – reading the potentiometer for output frequency
- AD1 – reading the buttons used for controller operation
- AD2 – current measurement
- AD3 – voltage measurement
Output pins:
- Pin 32 (releykon) – enables the mains capacitor relay
- Pin 35 (releynapR) – enables the controller supply relay
- Pin 34 (releynap0) – enables the controller supply relay
- Pin 33 (enableIGBT) – controls the switching of output transistors
- Pin 36 (kontrola) – checks the interrupt frequency of Timer 1
- Pin 46 (FAZA_U) – PWM output pin
- Pin 45 (FAZA_V) – PWM output pin
- Pin 44 (FAZA_W) – PWM output pin

### 7.2 Main loop

After the system initialization, the program enters the loop and the controller is in stop mode (Figure 18). By pressing one of the tasteri, Taster_Levo or Taster_Desno, the motor starts rotating in the direction corresponding to the selected taster (Figures 19 and 20).

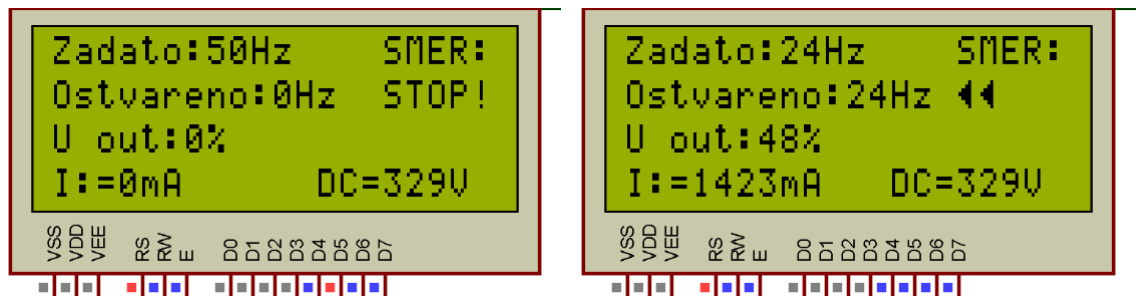
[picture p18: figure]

Figure 18. Stop | Figure 19. Left direction

Figure 20. Right direction

When the controller is in stop mode, by pressing Taster_Stop/Podеšavanje for more than two
seconds, | the | program | enters | the | settings | menu | (Figure | 21).
Here we adjust the limits for overvoltage and undervoltage protection, current limits, motor output frequency, acceleration and deceleration ramps, and the nominal motor frequency. With Taster_Gore and Taster_Dole we change the values of the selected parameters, while with Taster_Levo and Taster_Desno we select the parameter we want to modify. By pressing Taster_Stop/Podеšavanje again for more than two seconds, the parameters are written into the EEPROM and the program returns to the main loop.

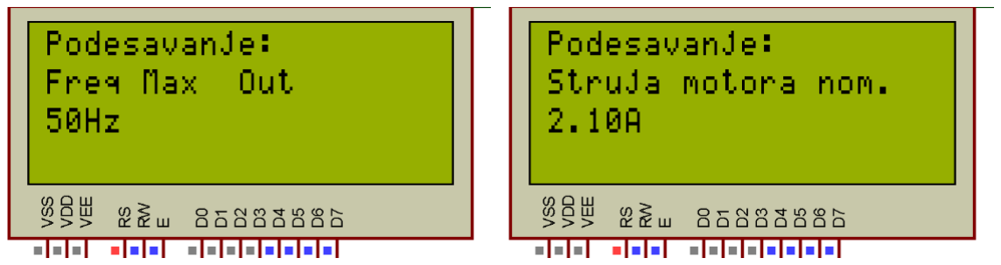
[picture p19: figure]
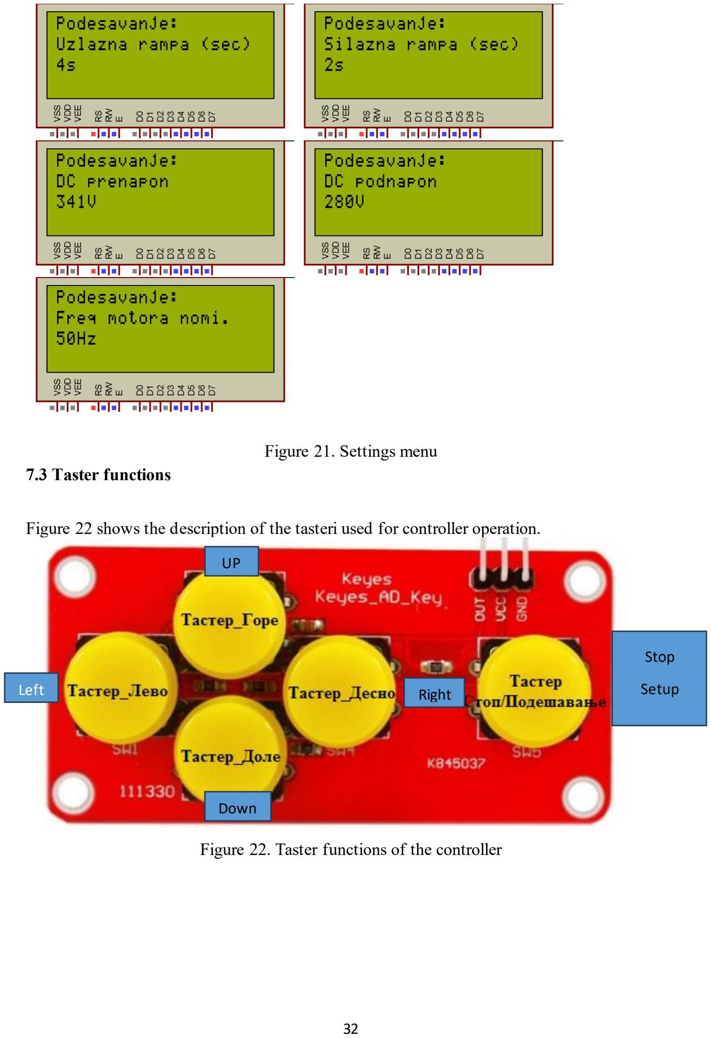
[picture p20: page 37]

Figure 21. Settings menu

### 7.3 Taster functions

Figure 22 shows the description of the tasteri used for controller operation.

Figure 22. Taster functions of the controller

Left

UP

Down

Right

Stop

Setup

## Three-phase SPWM signal generato

### 8. Simulation in MATLAB

Since a high-quality oscilloscope was not available for this work, a simulation was carried out in MATLAB with approximate values of voltage, frequency, and the switching frequency of the PWM signal. The project is included on the CD attached to this thesis.

The simulation schematic is shown in Figures 23 and 24.

Figure 23. PWM signal generation in MATLAB

Figure 24. Output stage in MATLAB

### 8.1 Waveforms of PWM signals

The following graphs show the waveforms of the PWM signal generator as well as the output voltages and currents simulated in MATLAB.

Graph 1. PWM signal waveforms in MATLAB

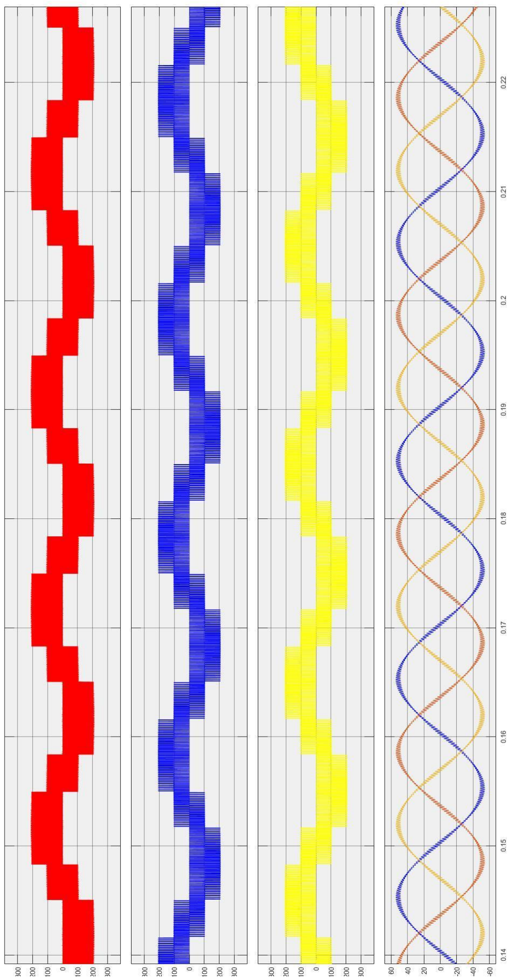
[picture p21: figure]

Graph 2. Output voltage and current waveforms (Phase-to-Ground measurement)

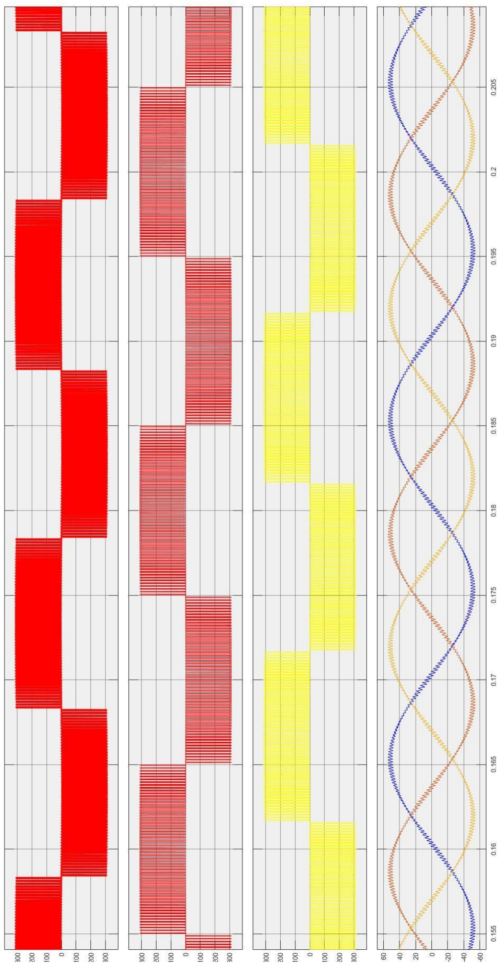
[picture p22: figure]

Graph 2. Output voltage and current waveforms (Phase-to-Phase measurement)

### 9. Conclusion

With this work, we have covered only a small part of the vast field of induction machine control. This is the simplest method of controlling a three-phase asynchronous motor. Scalar control of an asynchronous motor using the V/F technique is very easy to implement in practice, inexpensive, and reliable, but it has limitations regarding the applications where the motor can be used. It is most commonly applied in drives such as pumps, fans, and compressors, i.e., where motors operate with a constant torque, and several motors can be connected in parallel and regulated with a single controller. Thanks to the rapid advancement of electronic components and their relatively low cost, it is now much easier to implement more complex control methods of asynchronous motors, such as Space Vector Modulation (SVPWM) or Direct Torque Control (DTC), but these will be discussed in more detail in another work.

### 10. References

Predrag B. Petrović – Power Electronics
Radojle Radetić – Transistor Converters
Martin Brown – Electronics for Motor Drive and Control Language Reference – https://www.arduino.cc/reference/en/ Vladimir Petrović – Electrical Machines 2
www.google.com

### 11. Appendices

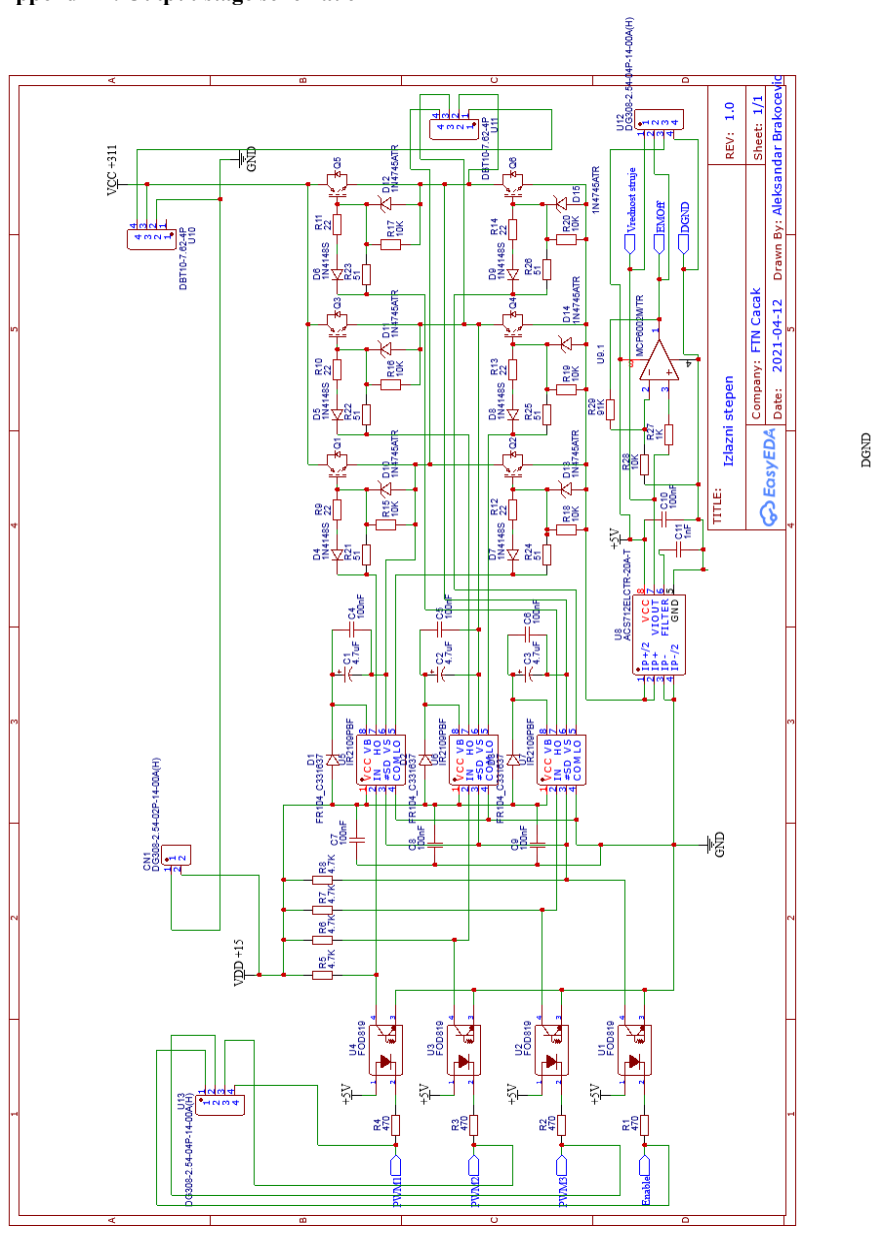
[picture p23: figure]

Appendix 1. Output stage schematic

Appendix 2. Arduino Mega 2560

Appendix 4. PCB layout (top side) – inverter output board

Appendix 4. PCB layout (bottom side) – inverter output board

*The Gerber file of the printed circuit boards is included on the attached CD.

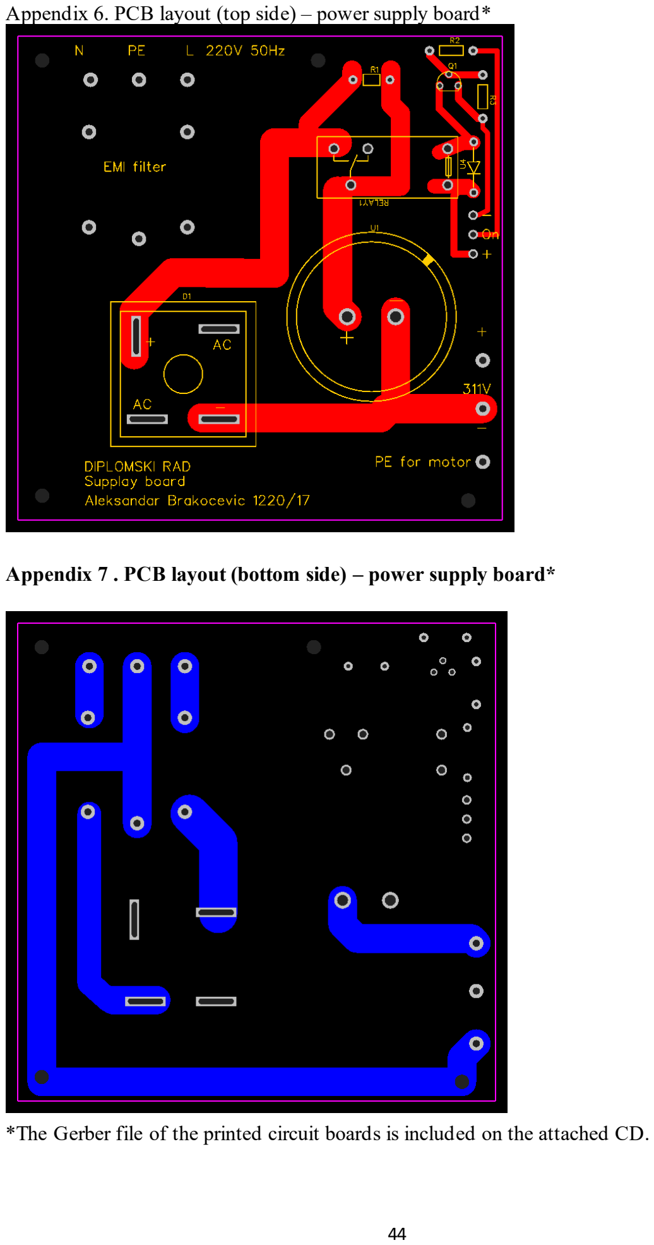
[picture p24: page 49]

Appendix 6. PCB layout (top side) – power supply board*

Appendix 7 . PCB layout (bottom side) – power supply board*

*The Gerber file of the printed circuit boards is included on the attached CD.

Appendix 8. Arduino program listing and Arduino code

It is included on the disk attached to the thesis.

Appendix 9. Technical specifications of Arduino Mega 2560

It is included on the disk attached to the thesis.

Appendix 10. Bill of Materials (BOM)

It is included on the disk attached to the thesis.

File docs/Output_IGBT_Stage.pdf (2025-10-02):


41

Appendix 1. Output stage schematic

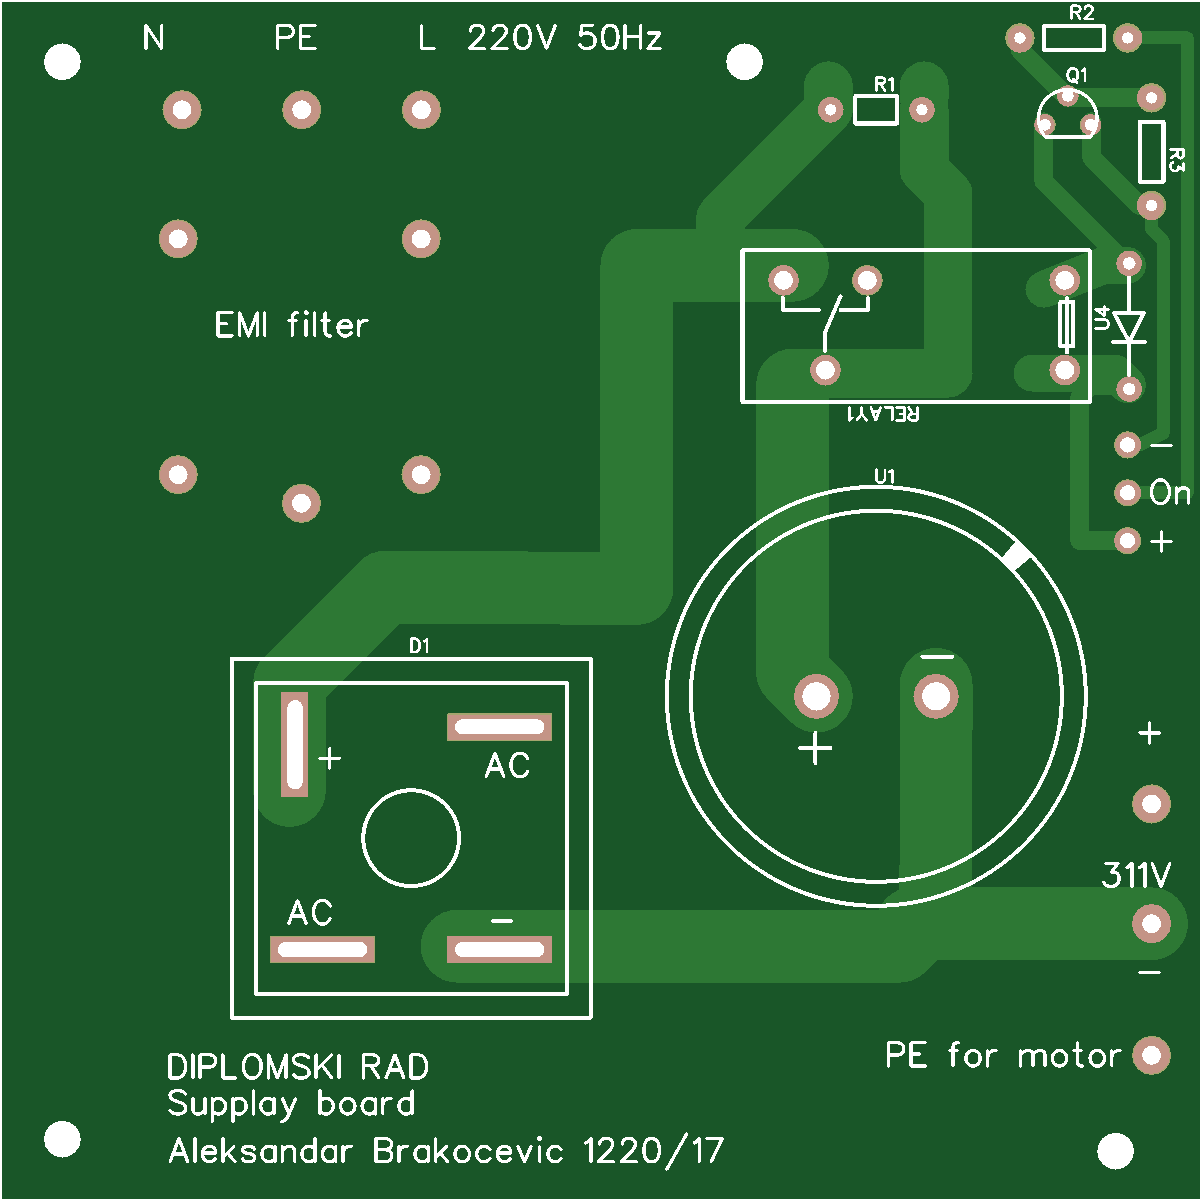
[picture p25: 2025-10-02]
hardware/PCB/Supplay_top.png

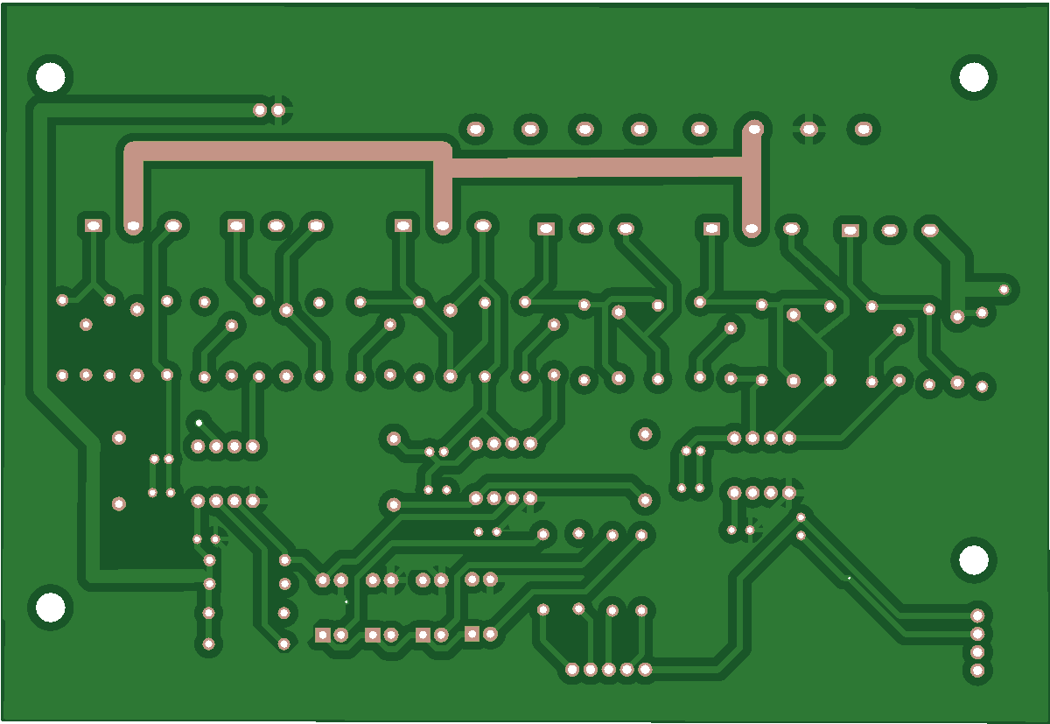
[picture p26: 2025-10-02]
hardware/PCB/PCB_IGBT_bottom.png

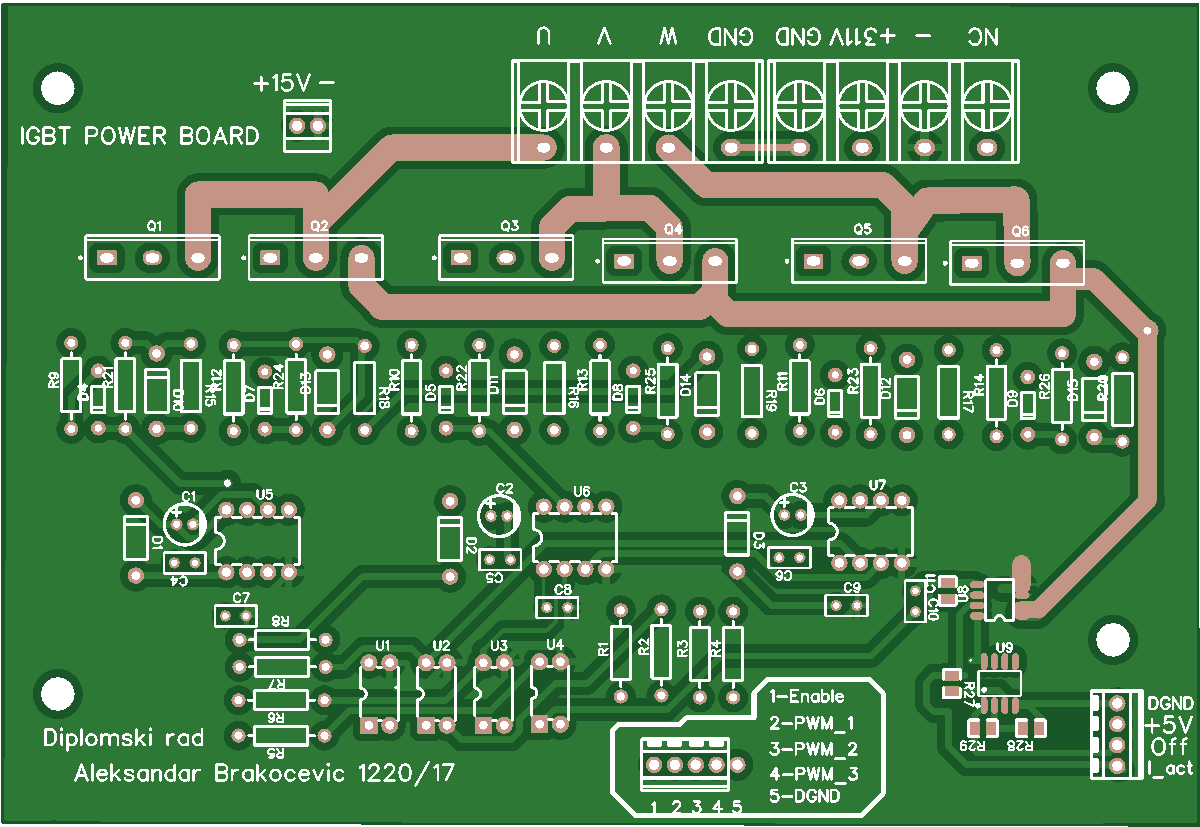
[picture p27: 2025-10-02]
hardware/PCB/PCB_IGBT_top.png

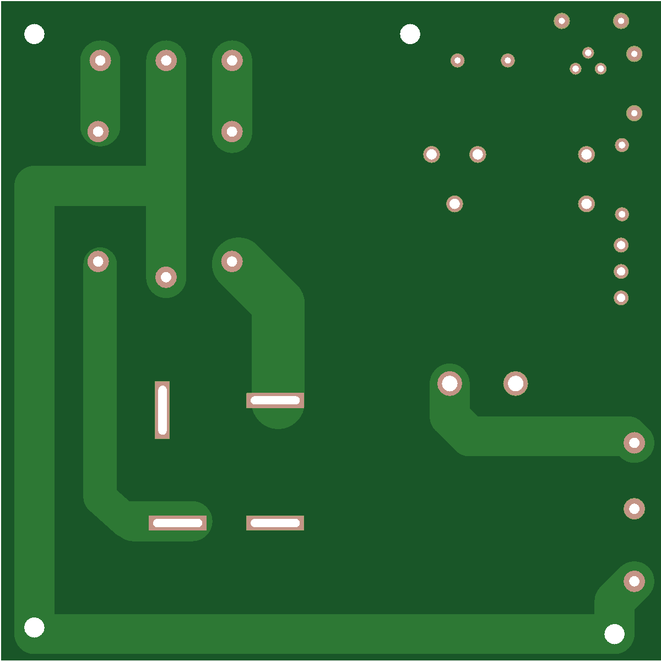
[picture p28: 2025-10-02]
hardware/PCB/Supplay_bottom .png

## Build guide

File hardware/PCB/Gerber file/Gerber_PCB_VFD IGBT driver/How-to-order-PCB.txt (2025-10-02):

How to Order PCB

Please refer to:
https://docs.easyeda.com/en/PCB/Order-PCB

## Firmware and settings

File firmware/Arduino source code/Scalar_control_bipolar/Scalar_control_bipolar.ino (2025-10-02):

#include <Wire.h>
#include <LiquidCrystal.h>
#include <ACS712.h>
#include <avr/pgmspace.h>
#include <EEPROM.h>

const int rs = 22, en = 23, d4 = 24, d5 = 25, d6 = 26, d7 = 27;
LiquidCrystal lcd(rs, en, d4, d5, d6, d7);
ACS712 ACS(A2, 5.0, 1023, 100);

// Arduino Mega has 5.0 volts max ADC value of 1023 steps
// ACS712 5A  uses 185 mV per A   //
// ACS712 20A uses 100 mV per A  // Constants for ASC712 depending on the type
// ACS712 30A uses 66 mV per A   //


volatile uint8_t numR;  // pointer to the value in the sine table
bool smer = false;      // flag for direction animation
int Animacija;          // variable for animation
int Flag_tajmer_za_mer_napona = 0;
float Amp;                      // variable for amplitude
int freq;                       // reading AD0 gives frequency
float napon;                    // variable for voltage measurement
int DC_MAX;                     // overvoltage
int DC_MIN;                     // undervoltage
int I_MAX;                      // maximum current
float I_MAX_eeprom;             // store maximum current in EEPROM
int adresa_float_struja = 8;    // EEPROM address for current
int freq_motora_nom;            // motor frequency from nameplate 50–60 Hz
long mA;                        // current measurement
long mA_temp;                   // current measurement
long mA_temp1;                  // current measurement
long mA_Prikaz;                 // current measurement (to display)
float freqF;                    // calculation of output frequency
float dfreq;                    // calculation of output frequency
float freqregulatora;           // calculation of output frequency
float freqscala;                // calculation of output frequency
int PhasaR;                     // Output phase R
int PhasaS;                     // Output phase S
int PhasaT;                     // Output phase T
int releykon = 32;              // pin for switching on mains capacitor relay
int releynapR = 35;             // pin for switching on voltage relay
int releynap0 = 34;             // pin for switching on voltage relay
int enableIGBT = 33;            // block/unblock output transistors
int kontrola = 36;              // frequency control
float speedup = 7;              // min frequency
int rampa_gore;                 // variable for acceleration
int rampa_dole;                 // variable for deceleration
bool flag_podesavanje = false;  // flag for entering settings
int izbor_ekrana = 6;           // number of items for settings
bool flag_ekran = false;        // variable for settings
bool strujna_zastita = false;   // overcurrent protection
int eeprom_prazan;              // EEPROM check
///////////////////////////////

//////////////////////////////////////////////////////////////
int naponsum = 0;           //
int napon_uzorak_broj = 0;  // voltage measurement
////////////////////////////////////////////////////////////
int KeyNumber;             //
int LCD_Buttons_ADC;       //
volatile byte StateVar;    // Variables for keyboard and direction status
volatile int Revers;       //
volatile byte LCD_Button;  //
//////////////////////////////////////////////////////////

//////////////////////////////////////////////
volatile byte PWM_Soft_A;  //
volatile byte PWM_Soft_B;  // Temporary register for PWM duration values
volatile byte PWM_Soft_C;  //
//////////////////////////////////////////////

////////////////////////////////////////////////////
volatile word phaseShiftA = 0;  //
volatile word phaseShiftB = 0;  // Variables for changing rotation direction
volatile word phaseShiftC = 0;  //
///////////////////////////////////////////////////

int start = 0;            // regulator status
#define NAPON_UZORAKA 10  // voltage measurement
#define R_0 46            //
#define S_0 45            // Output pins U-V-W
#define T_0 44            //
////////////////////////////////////////////// Assigning PWM registers to variables (U-V-W)
#define FAZA_U OCR5A
#define FAZA_V OCR5B
#define FAZA_W OCR5C
////////////////////////////////////////////
#define FREQ_POT A0  // analog input for output frequency
int FREQ_MIN = 7;    // default: 0
int FREQ_MAX = 50;   // default: 50
#define POT_MIN 0
#define POT_MAX 1023  // default: 1023

///////////////////////////////////////////////////////////////////////////////////////
// character for LCD direction left
byte levo[8] = {
  0x02, 0x06, 0x0E, 0x1E, 0x0E, 0x06, 0x02, 0x00
};
// character for LCD direction right
byte desno[8] = {
  0x08, 0x0C, 0x0E, 0x0F, 0x0E, 0x0C, 0x08, 0x00
};
//////////////////////////////////////////////////////////////////////////////////////

////////////////////////////////////////////////////////////////////////////////////////////////////////////////////// Three sine tables with 120° offset
const byte PROGMEM sine[][39] = {
  { 1, 4, 9, 16, 24, 34, 45, 57, 70, 83, 96, 109, 121, 132, 142, 150, 157, 162, 165, 166, 165, 162, 157, 150, 142, 132, 121, 109, 96, 83, 70, 57, 45, 34, 24, 16, 9, 4, 1 },
  { 132, 142, 150, 157, 162, 165, 166, 165, 162, 157, 150, 142, 132, 121, 109, 96, 83, 70, 57, 45, 34, 24, 16, 9, 4, 1, 1, 4, 9, 16, 24, 34, 45, 57, 70, 83, 96, 109, 121 },
  { 121, 109, 96, 83, 70, 57, 45, 34, 24, 16, 9, 4, 1, 1, 4, 9, 16, 24, 34, 45, 57, 70, 83, 96, 109, 121, 132, 142, 150, 157, 162, 165, 166, 165, 162, 157, 150, 142, 132 },
};
//////////////////////////////////////////////////////////////////////////////////////////////////////////////////////////////////////////////////////////////////////////////////////////////////////////////////////////////////

void setup() {
  pinMode(kontrola, OUTPUT);      // frequency control
  digitalWrite(kontrola, LOW);    // frequency control
  pinMode(enableIGBT, OUTPUT);    // protection against unwanted start
  digitalWrite(enableIGBT, LOW);  // force LOW state of digital output
  pinMode(releynapR, OUTPUT);     // relay for switching on voltage
  digitalWrite(releynapR, HIGH);
  pinMode(releynap0, OUTPUT);  // relay for switching on voltage
  digitalWrite(releynap0, HIGH);
  pinMode(releykon, OUTPUT);  // relay for switching on capacitor
  digitalWrite(releykon, LOW);
  lcd.createChar(0, levo);   // creating character for left direction display
  lcd.createChar(1, desno);  // creating character for right direction display

  lcd.begin(20, 4);
  // Print a message to the LCD.
  lcd.setCursor(0, 0);
  lcd.print(" Fakultet tehnickih");
  lcd.setCursor(3, 1);
  lcd.print("nauka u Cacku");
  lcd.setCursor(3, 2);
  lcd.print("Univerziteta u");
  lcd.setCursor(4, 3);
  lcd.print("Kragujevcu");
  delay(100);
  lcd.clear();
  lcd.setCursor(3, 0);
  lcd.print("Diplomski rad:");
  lcd.setCursor(0, 1);
  lcd.print("Skalarno upravljanje");
  lcd.setCursor(0, 2);
  lcd.print("karakter. trofaznog");
  lcd.setCursor(1, 3);
  lcd.print("asinhronog motora");
  delay(100);
  lcd.clear();
  lcd.setCursor(0, 0);
  lcd.print("Aleksandar");
  lcd.setCursor(0, 1);
  lcd.print("Brakocevic");
  lcd.setCursor(0, 2);
  lcd.print("broj indeksa:");
  lcd.setCursor(0, 3);
  lcd.print("1220/17");
  delay(100);
  lcd.clear();
  /////////////////////////////////////////////////////////// EEPROM check after system reset and writing parameters into working registers
  eeprom_prazan = EEPROM.read(0);
  if (eeprom_prazan == 255) {
    flag_podesavanje = true;
    podesavanje();
  }
  FREQ_MAX = EEPROM.read(1);
  rampa_gore = EEPROM.read(2);
  rampa_dole = EEPROM.read(3);

  DC_MAX = citanje_INT_from_eeprom(4);
  DC_MIN = citanje_INT_from_eeprom(6);
  freq_motora_nom = EEPROM.read(8);
  I_MAX = citanje_INT_from_eeprom(9);
  ////////////////////////////////////////////////////////////
  lcd.setCursor(0, 0);
  lcd.print("  Current sensor");
  lcd.setCursor(5, 1);
  lcd.print("calibration");
  ACS.autoMidPoint();
  delay(200);
  lcd.setCursor(7, 2);
  lcd.print("OK!!!");
  delay(200);

  lcd.clear();
  lcd.setCursor(0, 0);
  lcd.print("Switching voltage on");
  delay(200);
  digitalWrite(releynapR, LOW);
  digitalWrite(releynap0, LOW);
  delay(200);
  //lcd.setCursor(0,2);

  //lcd.print("OK!!!");
  delay(200);
  lcd.setCursor(0, 2);
  lcd.print("Capacitor charging");

  delay(200);
  digitalWrite(releykon, HIGH);
  lcd.clear();
  lcd.setCursor(0, 1);
  lcd.print("Voltage check!!!");
  delay(200);
  lcd.setCursor(7, 3);
  lcd.print("        !!!");
  merenje_DCnapon();
provera_napona:
  delay(200);
  if (napon < DC_MIN) {
    digitalWrite(releynapR, LOW);
    digitalWrite(releynap0, HIGH);
    lcd.clear();
    lcd.setCursor(0, 0);
    lcd.print("DC voltage below ");
    lcd.setCursor(0, 1);
    lcd.print("limit!!!");
    lcd.setCursor(0, 2);
    lcd.print("Turn off breaker");
    lcd.setCursor(0, 3);
    lcd.print("and check supply.");
    delay(100);
    goto provera_napona;
  }
  if (napon > DC_MAX) {
    digitalWrite(releynapR, LOW);
    digitalWrite(releynap0, HIGH);
    lcd.clear();
    lcd.setCursor(0, 0);
    lcd.print("DC voltage above ");
    lcd.setCursor(0, 1);
    lcd.print("limit!!!");
    lcd.setCursor(0, 2);
    lcd.print("Turn off breaker");
    lcd.setCursor(0, 3);
    lcd.print("and check supply.");
    delay(1000);
    goto provera_napona;
  } else

    delay(200);
  lcd.clear();
  lcd.setCursor(3, 1);
  lcd.print("SYSTEM READY!!!");
  delay(500);

  pinMode(R_0, OUTPUT);  // PWM 3A R_0

  pinMode(T_0, OUTPUT);  // PWM 3C S_0

  pinMode(S_0, OUTPUT);  // PWM 4B T_0

  lcd.clear();


  cli();                // stop interrupts
                        ////////////////////////////////////////////////////////////////////////////////////////////////////////////////////////////////////////
  TCCR5A = 0b10101010;  // phase-correct PWM mode // Description is in the diploma thesis
  TCCR5B = 0b00010010;  // no prescaler // Description is in the diploma thesis
  ICR5 = 166;
  OCR5A = 0;
  OCR5B = 0;  // Timer 5 settings
  OCR5C = 0;
  /////////////////////////////////////////////////////////////////////////////////////////////////////////////////////////////////
  // timer 1 settings
  TCCR1A = 0;           // reset the value
  TCCR1B = 0;           // reset the value
  TCNT1 = 0;            // reset the value
  OCR1A = 58608;        // initial value
  TCCR1B = 0b00001001;  // WGM12 bit is 1 for CTC mode and no prescaler
  ////////////////////////////////////////////////////////////////////////////
  // timer 3 settings
  TCCR3A = 0;   // reset the value
  TCCR3B = 0;   // reset the value
  TCNT3 = 0;    // reset the value
  OCR3A = 400;  //

  TCCR3B = 0b00001100;  // WGM12 bit is 1 for CTC mode without prescaler

  TIMSK1 |= (1 << OCIE1A);  // enable interrupts timer 1
  TIMSK3 |= (1 << OCIE3A);  // enable interrupts timer 3
  sei();                    //
}
////////-------------------------------------------------
ISR(TIMER1_COMPA_vect) {  // interrupt when timer 1 reaches OCR1A value
  digitalWrite(kontrola, !digitalRead(kontrola));
  if (StateVar == 0) { speedup = 0; }
  if (StateVar == 0) {
    cli();
    Motor_stop();
  }


  if (Amp > 1) {
    Amp = 1;
  }
  switch (StateVar) {
    case 0:
      PWM(phaseShiftA, phaseShiftB, phaseShiftC);
      break;
    case 1:
      phaseShiftA = 0;
      phaseShiftB = 1;
      phaseShiftC = 2;
      PWM(phaseShiftA, phaseShiftB, phaseShiftC);
      break;
    case 2:
      phaseShiftA = 0;
      phaseShiftB = 2;
      phaseShiftC = 1;
      PWM(phaseShiftA, phaseShiftB, phaseShiftC);
      break;
  }
}
void PWM(byte phaseShiftA, byte phaseShiftB, byte phaseShiftC) {
  // Refreshing the PWM registers
  PWM_Soft_A = ((pgm_read_byte_near(sine[phaseShiftA] + numR)) * Amp);  // Phase U update + amplitude
  PWM_Soft_B = ((pgm_read_byte_near(sine[phaseShiftB] + numR)) * Amp);  // Phase V update + amplitude
  PWM_Soft_C = ((pgm_read_byte_near(sine[phaseShiftC] + numR)) * Amp);  //  Phase W update + amplitude

  if (++numR > 38) {
    numR = 0;
  }


  FAZA_U = (PWM_Soft_A);
  FAZA_V = (PWM_Soft_B);
  FAZA_W = (PWM_Soft_C);

  OCR1A = freqscala;

  digitalWrite(kontrola, !digitalRead(kontrola));
}
ISR(TIMER3_COMPA_vect) {  // interrupt when timer 3 reaches OCR3A value
  if (start == 1) {
    OCR3A = 300 + (rampa_gore * 200);
    if (speedup < dfreq) {

      speedup = speedup + 0.25;
    }

    if (speedup > dfreq) {
      speedup = speedup - 0.25;
    }
  }
  if (start == 0) {
    OCR3A = 300 + (rampa_dole * 200);
    speedup = speedup - 0.25;
  }
}
void brzina() {
  freqregulatora = 1 / (1 / speedup / 39);
  freqscala = 16000000 / freqregulatora;
}



///////////////////////////////////////////////////////////////////////////////////////////////
void pisanje__citanje_INT_eeprom(int adress, int number) {
  EEPROM.write(adress, number >> 8);
  EEPROM.write(adress + 1, number & 0xFF);
}
int citanje_INT_from_eeprom(int adress) {
  return (EEPROM.read(adress) << 8) + EEPROM.read(adress + 1);
}
//////////////////////////////////////////////////////////////////////////////////////////////
void merenje_DCnapon() {
  while (napon_uzorak_broj < NAPON_UZORAKA) {
    naponsum += analogRead(A3);
    napon_uzorak_broj++;
    delay(1);
  }
  napon = ((float)naponsum / (float)napon_uzorak_broj * 5.0) / 1024.0;
  napon = (napon * 113.71);
  lcd.setCursor(12, 3);
  lcd.print("DC=");
  lcd.print(int(napon));
  lcd.print("V   ");
  naponsum = 0;
  napon_uzorak_broj = 0;
}

void prikaz() {
  lcd.setCursor(0, 0);
  lcd.print("Zadato:");
  lcd.print(int(dfreq));
  lcd.print("Hz ");
  lcd.setCursor(15, 0);
  lcd.print("SMER:");
  lcd.setCursor(15, 2);
  //lcd.print(Animacija);//(LCD_Buttons_ADC);
  lcd.print(" ");
  lcd.setCursor(0, 1);
  lcd.print("Ostvareno:");
  if (speedup >= 7) {
    lcd.print(round(speedup));
    lcd.print("Hz ");
  }
  if (speedup <= 7) {
    lcd.setCursor(0, 1);
    lcd.print("Ostvareno:");
    lcd.print("0");
    lcd.print("Hz ");
  }
  if (speedup >= 7) {
    lcd.setCursor(0, 2);
    lcd.print("U out:");
    lcd.print(int(Amp * 100));
    lcd.print("% ");
  }
  if (speedup <= 7) {
    lcd.setCursor(0, 2);
    lcd.print("U out:");
    lcd.print("0");
    lcd.print("% ");
  }
  lcd.setCursor(0, 4);
  lcd.print("I:");
  lcd.print(mA_Prikaz);
  lcd.print("mA   ");


  if (StateVar == 0) {
    lcd.setCursor(15, 1);
    lcd.print("STOP!");
  }
  if (StateVar == 1) {
    if (smer == true) {
      lcd.setCursor(15, 1);
      lcd.print("     ");
      lcd.setCursor(17, 1);
      lcd.print((char)0x00);
      lcd.print((char)0x00);
    }
    if (smer == false) {
      lcd.setCursor(15, 1);
      lcd.print("     ");
      lcd.setCursor(15, 1);
      lcd.print((char)0x00);
      lcd.print((char)0x00);
    }
  }
  if (StateVar == 2) {
    if (smer == true) {
      lcd.setCursor(15, 1);
      lcd.print("     ");
      lcd.setCursor(15, 1);
      lcd.print((char)0x01);
      lcd.print((char)0x01);
    }
    if (smer == false) {
      lcd.setCursor(15, 1);
      lcd.print("     ");
      lcd.setCursor(17, 1);
      lcd.print((char)0x01);
      lcd.print((char)0x01);
    }
  }
}

void citanje_tastera() {

  LCD_Buttons_ADC = analogRead(A1);                // read the buttons
  if (LCD_Buttons_ADC > 1000) LCD_Button = 0;      // button NONE
  else if (LCD_Buttons_ADC < 50) LCD_Button = 3;   // button RIGHT
  else if (LCD_Buttons_ADC < 195) LCD_Button = 1;  // button UP
  else if (LCD_Buttons_ADC < 380) LCD_Button = 2;  // button DOWN
  else if (LCD_Buttons_ADC < 555) LCD_Button = 4;  // button LEFT
  else if (LCD_Buttons_ADC < 790) LCD_Button = 5;  // button SELECT
  else LCD_Button = 0;
}
void loop() {

  citanje_tastera();


  freq = map(analogRead(FREQ_POT), POT_MIN, POT_MAX, FREQ_MIN, FREQ_MAX);
  Amp = speedup / freq_motora_nom;  //50;//50 motor frequency
  freqF = freq;
  dfreq = freqF;

  prikaz();


  if (Flag_tajmer_za_mer_napona == 26) {
    merenje_DCnapon();
    Flag_tajmer_za_mer_napona = 0;
  }
  Flag_tajmer_za_mer_napona++;

provera_napona1:
  if (napon < DC_MIN) {
    digitalWrite(enableIGBT, LOW);
    StateVar = 0;
    Revers = 0;
    TCCR5A = 0;
    TCCR5B = 0;
    speedup = 7;
    start = 0;
    digitalWrite(releynapR, LOW);
    digitalWrite(releynap0, HIGH);
    lcd.clear();
    lcd.setCursor(0, 0);
    lcd.print("DC voltage below ");
    lcd.setCursor(0, 1);
    lcd.print("limit!!!");
    lcd.setCursor(0, 2);
    lcd.print("Turn off breaker");
    lcd.setCursor(0, 3);
    lcd.print("and check supply.");
    delay(1000);
    goto provera_napona1;
  }
  if (napon > DC_MAX) {
    digitalWrite(enableIGBT, LOW);
    StateVar = 0;
    Revers = 0;
    TCCR5A = 0;
    TCCR5B = 0;
    speedup = 7;
    start = 0;
    digitalWrite(releynapR, LOW);
    digitalWrite(releynap0, HIGH);
    lcd.clear();
    lcd.setCursor(0, 0);
    lcd.print("DC voltage above ");
    lcd.setCursor(0, 1);
    lcd.print("limit!!!");
    lcd.setCursor(0, 2);
    lcd.print("Turn off breaker");
    lcd.setCursor(0, 3);
    lcd.print("and check supply.");
    delay(1000);
    goto provera_napona1;
  }
  mA = ACS.mA_AC();

  if (mA > I_MAX) {
    start = 0;

    strujna_zastita = true;
  } else {
    strujna_zastita = false;
  }
  if (strujna_zastita == true) {
    StateVar = 0;
    Revers = 0;
    TCCR5A = 0;
    TCCR5B = 0;
    speedup = 7;
    start = 0;
    delay(500);
    lcd.clear();
    lcd.setCursor(0, 0);
    lcd.print("Overcurrent");
    lcd.setCursor(0, 1);
    lcd.print("protection activated");
    lcd.setCursor(0, 2);
    lcd.print("Turn off breaker,");
    lcd.setCursor(0, 3);
    lcd.print("check motor.");
    delay(500);
    lcd.clear();
  }

  mA_temp = mA_temp + mA;

  if (mA_temp1 > 20) {
    mA_Prikaz = mA_temp / mA_temp1;
    mA_temp = 0;
    mA_temp1 = 0;
  }
  mA_temp1++;
  if (Revers == 0) {
    if (LCD_Button == 5)  // Stop
    {
      start = 0;
    }
    if (LCD_Button == 5 && StateVar == 0 && Animacija == 20) {
      flag_podesavanje = true;
      podesavanje();
    }



    if (speedup < 7) {
      digitalWrite(enableIGBT, LOW);
      StateVar = 0;
      Revers = 0;
      TCCR5A = 0;
      TCCR5B = 0;
      speedup = 7;
      start = 0;
    }
    if (LCD_Button == 3 && StateVar == 0 && start == 0)  // Forward
    {
      digitalWrite(enableIGBT, HIGH);
      speedup = 7;
      StateVar = 1;
      Revers = 0;
      start = 1;
      TCCR1B = 0b00001001;
      TCCR5A = 0b10101010;
      TCCR5B = 0b00010010;
    }                                                    //sei();}
    if (LCD_Button == 4 && StateVar == 0 && start == 0)  // Backward
    {
      digitalWrite(enableIGBT, HIGH);
      speedup = 7;
      StateVar = 2;
      Revers = 0;
      start = 1;
      TCCR1B = 0b00001001;
      TCCR5A = 0b10101010;
      TCCR5B = 0b00010010;
    }  //sei();}
  }

  brzina();
  dfreq = speedup;




  if (Animacija > 20) {

    smer = !smer;
    Animacija = 0;
  }
  Animacija++;
}
void Motor_stop() {
  TCCR1A = 0;  // reset the value
  TCCR1B = 0;  // reset the value
  TCNT1 = 0;   // reset the value
  TCCR5A = 0;
  TCCR5B = 0;
  speedup = 7;
  start = 0;
  numR = 0;
  phaseShiftA = 0;
  phaseShiftB = 0;
  phaseShiftC = 0;
}
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

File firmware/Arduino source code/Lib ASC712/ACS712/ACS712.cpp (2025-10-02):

//
//    FILE: ACS712.cpp
//  AUTHOR: Rob Tillaart, Pete Thompson
// VERSION: 0.2.1
//    DATE: 2020-08-02
// PURPOSE: ACS712 library - current measurement
//
// HISTORY:
// 0.1.0    2020-03-17 initial version
// 0.1.1    2020-03-18 first release version
// 0.1.2    2020-03-21 automatic formfactor test
// 0.1.3    2020-05-27 fix library.json
// 0.1.4    2020-08-02 Allow for faster processors
// 0.2.0    2020-08-02 Add autoMidPoint
// 0.2.1    2020-12-06 Add arduino-CI + readme + unittest + refactor

#include "ACS712.h"

ACS712::ACS712(uint8_t analogPin, float volts, uint16_t maxADC, uint8_t mVperA)
{
  _pin = analogPin;
  _mVpstep     = 1000.0 * volts / maxADC;  // 1x 1000 for V -> mV
  _mVperAmpere = mVperA;
  _formFactor  = 0.70710678119;  // 0.5 * sqrt(2);  TODO: should be smaller in practice 0.5 ?
  _midPoint    = maxADC / 2;
  _noisemV     = 21;             // Noise is 21mV according to datasheet
}

int ACS712::mA_AC(uint8_t freq)
{
  uint32_t start = micros();
  uint16_t period = ((freq == 60) ? 16670 : 20000);
  uint16_t samples = 0;
  uint16_t zeros = 0;

  int _min, _max;
  _min = _max = analogRead(_pin);

  while (micros() - start < period)  // UNO ~180 samples...
  {
    samples++;
    int val = analogRead(_pin);
    if (val < _min) _min = val;
    if (val > _max) _max = val;
    if (abs(val - _midPoint) <= (_noisemV/_mVpstep)) zeros++;
  }
  int point2point = (_max - _min);

  // automatic determine _formFactor / crest factor
  float D = 0;
  float FF = 0;
  if (zeros > samples * 0.025)
  {
    D = 1.0 - (1.0 * zeros) / samples;    // % SAMPLES NONE ZERO
    FF = sqrt(D) * 0.5 * sqrt(2);         // ASSUME NON ZERO PART ~ SINUS
  }
  else  // # zeros is small => D --> 1 --> sqrt(D) --> 1
  {
    FF = 0.5 * sqrt(2);
  }
  _formFactor = FF;

  // math could be partially precalculated: C = 1000.0 * 0.5 * _mVpstep / _mVperAmpere;
  // rounding?
  return 1000.0 * 0.5 * point2point * _mVpstep * _formFactor / _mVperAmpere;
}

long ACS712::mA_DC()
{
    // read twice to stabilize...
    analogRead(_pin);
    int steps = analogRead(_pin) - _midPoint;
    return 1000.0 * steps * _mVpstep / _mVperAmpere;
}

// configure by sampling for 2 cycles of AC
// Also works for DC as long as no current flowing
void ACS712::autoMidPoint(uint8_t freq)
{
  uint32_t start = micros();
  uint16_t twoPeriods = ((freq == 60) ? 16670 : 20000) * 2;
  uint32_t total = 0;
  uint32_t samples = 0;
  while (micros() - start < twoPeriods) {
    uint16_t reading = analogRead(_pin);
    total += reading;
    samples ++;
    // Delaying ensures we won't overflow since we'll perform a maximum of 40,000 reads
    delayMicroseconds(1);
  }
  _midPoint = total / samples;
}

// END OF FILE

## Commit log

2025-10-02 PCB files and layouts
2025-10-02 Arduino C source code
    INO File
2025-10-02 Arduino C source code
2025-10-02 Project documentation, schematics, calculations
